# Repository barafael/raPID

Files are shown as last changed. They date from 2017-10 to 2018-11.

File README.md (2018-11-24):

# raPID: Rafaels PID flight controller



This flight controller consists mostly of a teensy 3.2 and an EM-SENtral motion sensor board. The
teensy can read up to 8 PWM or PPM channels from your standard RC receiver (see
include/pins.h for input/output pin numbers). Each of the outputs can be driven
by a weighted sum of the roll, pitch, yaw PID responses and the throttle
channel. The remaining 4 channels are currently unused, but it would be simple
to use them to drive the outputs like the throttle channel does. This is a
matrix multiplication, conceptually. The matrix maps an input (RX, PID) to the
output.

Three inputs drive the PID setpoints. By default, a cascaded PID controller is
used - resulting in stabilize mode. The first controller gets the RX input and
the absolute attitude from the IMU sensor. It outputs the desired rate. This
rate is fed as the setpoint to another controller, which uses the faster gyro
measurements of angular rate as process value. This setup results in
stabilization mode (stick deviation sets vehicle attitude). Acro mode is
achieved by disabling the first controller (which will then just pass through
the setpoint to the next controller) and only using the rate controller.

## Features
- [x] Arming/disarming
- [x] Mixers for each output, applying differently weighted inputs and IMU data to the outputs
- [x] Rate/stabilize mode
- [x] Support several output waveforms
  - [x] Various output classes (Servo, ESC, anyPWM)
  - [x] 400Hz update rate for ESCs using analogWrite timers (to do: test it)
  - [x] Arbitrary PWM waveform generation to drive even LEDs
- [x] PID Improvements
  - [x] D noise filters: lowpass, moving average
  - [x] Derivative-on-{error, feedback, setpoint}
  - [ ] Fixed point PID implementation
  - [ ] [not needed right now] Calculating error external from algorithm or pass an ```errorfunc(number, number) -> number``` function pointer (more general)

## TODO
- [x] Fix serial monitor ritual (current: remove tx, reboot, wait for sermon, connect tx)
- [x] Fix gyro vs. fused and rate vs. stbl issues (-15 factor)
- [ ] Receiver
  - [x] Per-channel offsets to set zero/mid-points and somehow work around special case for throttle, which needs 50% extra offset
  - [ ] Fix PPM receiver read
- Outputs
  - [x] 400Hz PWM output test and fix
  - [ ] Rethink set_limits, general implementation of generic waveforms? Specialization in servo (endpoints, expo?, trimming, inversion). Maximum range must be at least standard max signal pulse width
- [ ] Safety Enhancements
  - [x] Make sure arming functionality works and is reliable
  - [ ] Add safety mechanisms for receiver signal loss (detect RX failsafe output)
  - [ ] Fix/Improve watchdog timer functionality. Is this even necessary? A software crash will likely lead to crash of vehicle, since the controller boots to disarmed mode. Check if wakeup from watchdog, then proceeding armed? Currently, watchdog is disabled
- [x] Increase IMU sensor sampling rates - 1kHz

## Ideas
- [ ] Airspeed-adjustable gains
- [ ] Live coefficient tweaking (standard tx or telemetry hardware)
  - [ ] RFM95 lora board for config data, telemetry
- [x] IMU solution overhaul: Ultimate SENtral or other; constant sampling rate simplifies PID and makes theory on time-discrete systems applicable
  - [x] General IMU interface class to test different IMU implementations
- [ ] Matrix multiplication for output coefficients (every output is some weighted sum of the inputs + PID response) Possibly use DSP instructions and SIMD - one microsecond for multiplying 8x12 and a 12 column vector is achievable
  - [ ] Weights in output matrix are only linear multiplication. Would it make sense to use a matrix of function pointers to support expo? Performance (inlining possible?)?
  - [ ] 8x12 x 12x1 int16_t matrix/vector multiplication with naive for loop implementation: 12us. Unrolled loops: 3us-6us. Sufficient, probably.
  - [ ] 8x12 x 12x1 float matrix-vector multiplication with unrolled loops: 170us. Insufficient.
- [ ] Arbitrary flight modes (different PID settings, offsets, and I/O matrix)
- [ ] Flight mode interpolation (otherwise called transitional mixers) to smoothly switch between any two flight modes
  - [ ] Flight mode matrix to other flight mode matrix: ```(1 - transition) * old_mat + transition * new_mat``` for now. Sine/other functions, duration of transition, etc. later.
  - [ ] How to support more complex transitions where linear is insufficient? Pass pointer to function that takes end and start points, and percent, and gives interpolation value:
        ```squared_sine(startpoint, endpoint, percent) -> interpolated```
- [ ] Adjust settings wirelessly, ideally using a desktop application/website (have not thought about that part yet... far off)
- [ ] Use an RTOS?
  * Periodic tasks that run slower than flight loop:
    * Arming/disarming toggle check
    * Flightmode matrix transition update
    * Telemetry
    * Watchdog
    * RX update (depending on mode(PPM, PWM)) lower frequency than flight loop
    * RX check if has_channel (or use RC RX failsafe mode to detect?) [can run at 5Hz]
    * Serial debug output (?)
  * As fast as possible
    * IMU read
    * PID loops
    * Flight mode matrix vector multiplication
    * ```output.apply(value)```

Blog-in-progress @ [https://barafael.github.io/Remote-Control-Vehicle-Balance-controller/](https://barafael.github.io/Remote-Control-Vehicle-Balance-controller/)

## Inspiration and Acknowledgments

* OpenAeroVTOL from the RCGroups forums, by HappySundays - awesome project.
* Jeff Rowberg's MPU6050 library and example code.

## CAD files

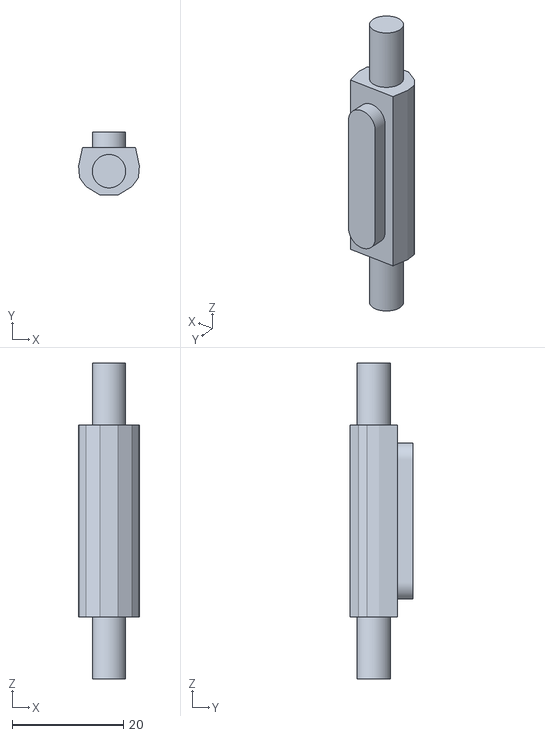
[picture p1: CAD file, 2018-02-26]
handle.stl
10.9 x 11.4 x 56.7

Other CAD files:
handle.blend

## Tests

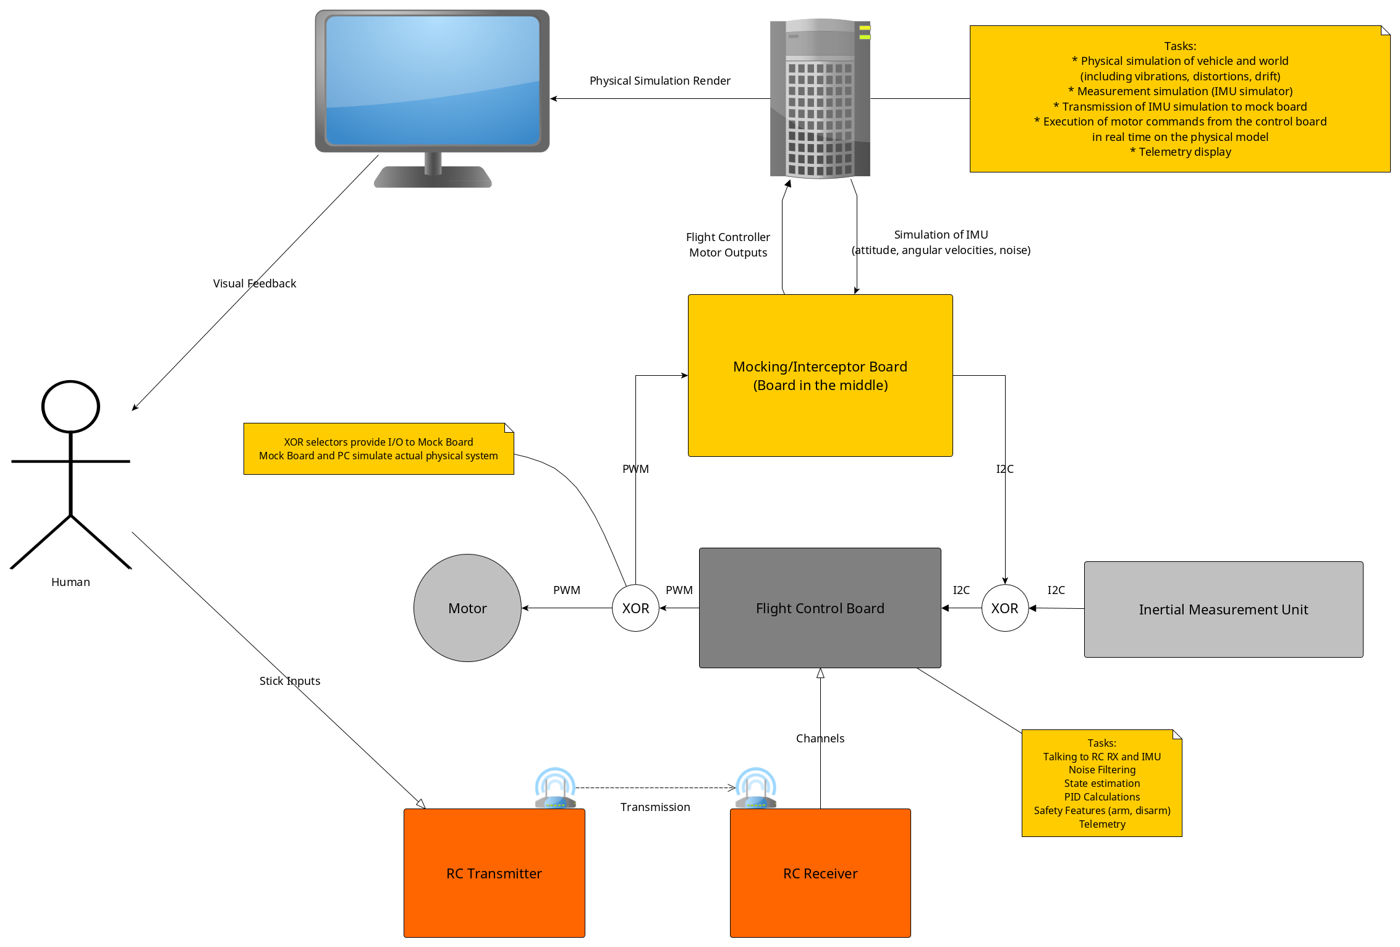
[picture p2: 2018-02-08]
controller_simulator_test_rig.png

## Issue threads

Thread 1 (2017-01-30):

Yaw readout drift [?]

barafael, 2017-01-30:
Yaw readout in Teensy_MPU6050_imu.ino is constantly increasing until it stabilizes after a while. Pitch and roll readouts are not affected. This could be a hardware issue, or a bug, or a wrong value set at   `mpu.setXGyroOffset(220);`
`mpu.setYGyroOffset(76);`
`mpu.setZGyroOffset(-85);`
`mpu.setZAccelOffset(1788);`

barafael, 2017-11-22:
https://www.i2cdevlib.com/forums/topic/10-why-is-the-dmp-yaw-stable/

Closed 2017-11-24.

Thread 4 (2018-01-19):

No need to wait after Wire.requestFrom()

Koepel, 2018-01-19:
In the file raPID/src/imu.cpp you can remove this line: `while (Wire.available() < 6) {}`. It is used twice.

The Wire.requestFrom() waits until the complete I2C transaction on the bus has finished. There is no need to wait for something after the call to Wire.requestFrom().
In case of a bus collision or an error that the Wire library could detect (it can not detect most problems), then the Wire.available() will probably return zero, and that loop will halt the sketch.

barafael, 2018-01-19:
Thanks for spotting that! I will remove the line. Awesome!

Koepel, 2018-01-19:
Thanks. That was fast.

You use the I2Cdev code, which is using the Wire library in a wrong way ( https://github.com/jrowberg/i2cdevlib/issues/265 ). That library is no longer maintained and the issues are piling up. The library is also a little outdated. Your copy of "init_mpu6050" is therefor also a little outdated. The FastWire option is not really needed and setting the TWBR for the speed is no longer needed, since there is a Wire.setClock() function now.

There is not much you or me can do about it. Keep in mind that the library is slower than needed, with extra unnecessary bus activity that slows it down. With the current version of the AVR Wire library the I2Cdev library works (despite the wrong use), so for now it is okay.

barafael, 2018-01-19:
I guess it would be possible to use the i2c_t3 library in I2Cdev, however as you said it could be a lot of work.

I have sufficient power on my microcontroller to be able to do my own sensor fusion, so [this library by Kris Winer](https://github.com/kriswiner/MPU6050) is worth looking at for me.
In the long run, I want to use a different sensor anyway, as InvenSense has presented really good new options as recent as CES.

Thank you for pointing out the issues!

Koepel, 2018-01-19:
You might consider to upgrade to the MPU-9250 and try the Kris Winer AHRS fusion. Sometimes a MPU-6050 module is shipped with a smaller capacitor which causes extra noise. The MPU-9250 doesn't have that capacitor.

barafael, 2018-01-19:
Ok, that sounds like it will improve the IMU quite a bit. I am wondering about the tradeoffs of using on-chip sensor fusion vs. doing it on the main board. I guess I will try both!

BTW, great job on helping all those other people use the Wire library correctly.

Closed 2018-01-19.

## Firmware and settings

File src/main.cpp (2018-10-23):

#include "Arduino.h"

#include <stdint.h>

//#define WATCHDOG

#include "../include/output/ESCOutput.hpp"
#include "../include/output/FastPWMOutput.hpp"
#include "../include/output/LEDOutput.hpp"
#include "../include/imu/axis.hpp"
#include "../include/pid/PIDController.hpp"
#include "../include/receiver/PWMReceiver.hpp"
#include "../include/receiver/PPMReceiver.hpp"
#include "../include/ArmingState.hpp"
#include "../include/error_blink.h"
#include "../include/pins.h"
#include "../include/imu/SENtralIMU.hpp"
#include "../include/settings.h"

#ifdef WATCHDOG
#include "../include/Watchdog.hpp"
#endif

#define TIMING_ANALYSIS
#ifdef TIMING_ANALYSIS
#define time(f)                          \
    {                                    \
        digitalWrite(DEBUG_PIN, HIGH);   \
        f;                               \
        digitalWrite(DEBUG_PIN, LOW);    \
    }
#else
#define time(f) f
#endif

#define notime(f) f


/*
   ----------------------------------------------
   ---             HARDWARE SETUP             ---
   ----------------------------------------------

   SENtral Breakout ----- Teensy 3.2
   3.3V ----------------- 15
   GND ------------------ 14
   SDA ------------------ A4/pin 18
   SCL ------------------ A5/pin 19
   INT ------------------ Digital Pin 6 (see pins.h)

   See ../include/pins.h for more pin definitions.
   */

/* Default start state */
state_t state = DISARMED;

/* Scaled yaw_pitch_roll to [0, 1000] */
//axis_t attitude = { 0, 0, 0 };
float attitude[3] = { 0 };

/* Angular Rate */
//axis_t angular_rates = { 0, 0, 0 };
float angular_rates[3] = { 0 };

float pid_output_roll_stbl = 0.0;
float pid_output_roll_rate = 0.0;

float pid_output_pitch_stbl = 0.0;
float pid_output_pitch_rate = 0.0;

float pid_output_yaw_rate = 0.0;

channels_t channels = { 0 };

static void print_attitude(axis_t attitude) {
    for (size_t index = 0; index < 3; index++) {
        Serial.print(attitude[index]);
        Serial.print(F("\t"));
    }
    Serial.println();
}

static void print_velocity(float *velocity) {
    for (size_t index = 0; index < 3; index++) {
        Serial.print(velocity[index]);
        Serial.print(F("\t"));
    }
    Serial.println();
}

static void print_velocity_max(axis_t velocity) {
    static int64_t max_velocity = 0;
    for (size_t index = 0; index < 3; index++) {
        if (velocity[index] > max_velocity || velocity[index] < -max_velocity) {
            max_velocity = velocity[index];
            Serial.println((long) max_velocity);
        }
    }
}

static void print_channels(channels_t channels) {
    for (size_t index = 0; index < NUM_CHANNELS; index++) {
        Serial.print(channels[index]);
        Serial.print(F("\t"));
    }
    Serial.println();
}

extern "C" int main(void) {
    pinMode(LED_PIN, OUTPUT);
    pinMode(DEBUG_PIN, OUTPUT);

    Serial.begin(9600);
    while(!Serial);

    int counter = 10;
    while(counter) {
        Serial.println("Hello");
        delay(500);
        digitalWrite(LED_PIN, !digitalRead(LED_PIN));
        counter--;
    }

    static bool blink_state = false;

    delay(1000);

    channels_t offsets = { -1000, -1500, -1500, -1500, -1500, -1500 };

    PWMReceiver receiver(THROTTLE_INPUT_PIN, ROLL_INPUT_PIN,
                         PITCH_INPUT_PIN,    YAW_INPUT_PIN,
                         AUX1_INPUT_PIN,     AUX2_INPUT_PIN,
                         offsets);
  
    //PPMReceiver receiver(23, offsets);

    while (!receiver.has_signal()) {
        delay(500);
        Serial.println(F("No receiver signal! Waiting."));
    }

    Serial.println(F("Receiver signal detected, continuing."));

    PIDParams roll_param_stbl ( 2.0 , 0.0 , 0.0 , 12.0 , 400.0);
    PIDParams roll_param_rate ( 0.65 , 0.0 , 0.0 , 12.0 , 400.0);

    PIDParams pitch_param_stbl( 2.0 , 0.0 , 0.0 , 12.0 , 400.0);
    PIDParams pitch_param_rate( 0.65 , 0.0 , 0.0 , 12.0 , 400.0);

    PIDParams yaw_param_rate  ( 1.5 , 0.0 , 0.0 , 12.0 , 400.0);

    PIDController roll_controller_stbl(roll_param_stbl);
    PIDController roll_controller_rate(roll_param_rate);

    PIDController pitch_controller_stbl(pitch_param_stbl);
    PIDController pitch_controller_rate(pitch_param_rate);

    PIDController yaw_controller_rate(yaw_param_rate);

    FastPWMOutput back_left_out_mixer  (LEFT_SERVO_PIN  , 1.0 , -1.0 , -1.0 , 1.0);
    FastPWMOutput back_right_out_mixer (RIGHT_SERVO_PIN , 1.0 , 1.0  , -1.0 , -1.0);
    FastPWMOutput front_left_out_mixer (FRONT_SERVO_PIN , 1.0 , -1.0 , 1.0  , -1.0);
    FastPWMOutput front_right_out_mixer(BACK_SERVO_PIN  , 1.0 , 1.0  , 1.0  , 1.0);

    back_left_out_mixer  .shut_off();
    back_right_out_mixer .shut_off();
    front_left_out_mixer .shut_off();
    front_right_out_mixer.shut_off();

    roll_controller_stbl.set_enabled(true);
    roll_controller_rate.set_enabled(true);

    pitch_controller_stbl.set_enabled(true);
    pitch_controller_rate.set_enabled(true);

    SENtralIMU sentral;

#ifdef WATCHDOG
    Watchdog dog;
#endif

    ArmingState arming_state(channels);

    /* Flight loop */
    while(true) {
        receiver.update(channels);
        //print_channels(channels);

        sentral.update_attitude(attitude);
        //print_attitude(attitude);

        sentral.update_angular_rates(angular_rates);
        //print_velocity(angular_rates);

        switch (arming_state.get_state()) {
            case ARMED:
                pid_output_roll_stbl = roll_controller_stbl.  compute(attitude[ROLL_AXIS], channels[ROLL_CHANNEL]);

                pid_output_roll_rate = roll_controller_rate.  compute(angular_rates[ROLL_AXIS], -pid_output_roll_stbl);

                //pitch_controller_stbl.set_p((channels[ROLL_CHANNEL] + 500) * (15.0 / 1000));
                //pitch_controller_stbl.set_i((channels[YAW_CHANNEL]  + 500) * (5.0  / 1000));

                //Serial.println(pitch_controller_stbl.get_p());
                //Serial.print("\t");
                //Serial.println(pitch_controller_stbl.get_d());

                pid_output_pitch_stbl = pitch_controller_stbl.compute(attitude[PITCH_AXIS], channels[PITCH_CHANNEL] / 10);

                pid_output_pitch_rate = pitch_controller_rate.compute(angular_rates[PITCH_AXIS], -pid_output_pitch_stbl);

                /* Yaw needs rate only - yaw stick controls rate of rotation, there is no fixed reference */
                pid_output_yaw_rate = yaw_controller_rate.    compute(angular_rates[YAW_AXIS], channels[YAW_CHANNEL]);

                back_left_out_mixer  .apply(channels[THROTTLE_CHANNEL], pid_output_roll_rate, pid_output_pitch_rate, pid_output_yaw_rate);
                back_right_out_mixer .apply(channels[THROTTLE_CHANNEL], pid_output_roll_rate, pid_output_pitch_rate, pid_output_yaw_rate);
                front_left_out_mixer .apply(channels[THROTTLE_CHANNEL], pid_output_roll_rate, pid_output_pitch_rate, pid_output_yaw_rate);
                front_right_out_mixer.apply(channels[THROTTLE_CHANNEL], pid_output_roll_rate, pid_output_pitch_rate, pid_output_yaw_rate);

                //#define DEBUG_COL
#ifdef DEBUG_COL
                Serial.print(F("setp:"));
                Serial.print(channels[ROLL_CHANNEL]);
                Serial.print(F("\troll-angl:"));
                Serial.print(attitude[ROLL_AXIS]);
                Serial.print(F("\tpid_output_roll_stbl:"));
                Serial.print(pid_output_roll_stbl);
                Serial.print(F("\tpid_output_roll_rate:"));
                Serial.println(pid_output_roll_rate);
#endif

                break;

            case DISARMED:
                back_left_out_mixer  .shut_off();
                back_right_out_mixer .shut_off();
                front_left_out_mixer .shut_off();
                front_right_out_mixer.shut_off();

                break;

            default:
                Serial.println(F("Unimplemented state! Will disarm."));
                state = DISARMED;
                break;
        }

        /* Blink LED to indicate activity */
        blink_state = !blink_state;
        digitalWrite(LED_PIN, blink_state);
#ifdef WATCHDOG
        dog.feed();
#endif
    }
}

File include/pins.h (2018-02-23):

#ifndef PINS_H
#define PINS_H

#include <stdint.h>

static const uint8_t DEBUG_PIN = 15;

static const uint8_t LED_PIN = 15;

static const uint8_t SENTRAL_GND = 13;
static const uint8_t SENTRAL_POWER = 14;

static const uint8_t SENTRAL_INTERRUPT_PIN = 8;

typedef enum {
    THROTTLE_INPUT_PIN = 22,
    ROLL_INPUT_PIN     = 20,
    PITCH_INPUT_PIN    = 21,
    YAW_INPUT_PIN      = 23,
    AUX1_INPUT_PIN     = 19,
    AUX2_INPUT_PIN     = 18,
} input_pin;

typedef enum {
    LEFT_SERVO_PIN  = 5,
    RIGHT_SERVO_PIN = 4,
    FRONT_SERVO_PIN = 3,
    BACK_SERVO_PIN  = 6
} output_pin;

#endif // PINS_H

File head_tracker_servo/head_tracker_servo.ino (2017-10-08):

/* ============================================
  I2Cdev device library code is placed under the MIT license
  Copyright (c) 2012 Jeff Rowberg

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
  THE SOFTWARE IS PROVIDED "AS IS", WITHOUT WARRANTY OF ANY KIND, EXPRESS OR
  IMPLIED, INCLUDING BUT NOT LIMITED TO THE WARRANTIES OF MERCHANTABILITY,
  FITNESS FOR A PARTICULAR PURPOSE AND NONINFRINGEMENT. IN NO EVENT SHALL THE
  AUTHORS OR COPYRIGHT HOLDERS BE LIABLE FOR ANY CLAIM, DAMAGES OR OTHER
  LIABILITY, WHETHER IN AN ACTION OF CONTRACT, TORT OR OTHERWISE, ARISING FROM,
  OUT OF OR IN CONNECTION WITH THE SOFTWARE OR THE USE OR OTHER DEALINGS IN
  THE SOFTWARE.
  ===============================================
*/

/* I2C device class (I2Cdev) demonstration Arduino sketch for MPU6050 class using DMP (MotionApps v2.0)
  6/21/2012 by Jeff Rowberg <jeff@rowberg.net>
  Updates should (hopefully) always be available at https://github.com/jrowberg/i2cdevlib

  Changelog:
      2013-05-08 - added seamless Fastwire support
                 - added note about gyro calibration
      2012-06-21 - added note about Arduino 1.0.1 + Leonardo compatibility error
      2012-06-20 - improved FIFO overflow handling and simplified read process
      2012-06-19 - completely rearranged DMP initialization code and simplification
      2012-06-13 - pull gyro and accel data from FIFO packet instead of reading directly
      2012-06-09 - fix broken FIFO read sequence and change interrupt detection to RISING
      2012-06-05 - add gravity-compensated initial reference frame acceleration output
                 - add 3D math helper file to DMP6 example sketch
                 - add Euler output and Yaw/Pitch/Roll output formats
      2012-06-04 - remove accel offset clearing for better results (thanks Sungon Lee)
      2012-06-01 - fixed gyro sensitivity to be 2000 deg/sec instead of 250
      2012-05-30 - basic DMP initialization working

      2017-01-10 - [Rafael Bachmann] add servo output (needs low pass filter such as capacitor in parallel for pwm to work)
      2017-01-30 - [Rafael Bachmann] modifications to run this sketch on the teensy 3.2
      2017-01-30 - [Rafael Bachmann] removal of teapot output
      2017-09-10 - [Rafael Bachmann] boil down to head tracker implementation with 0-calibration
*/

// I2Cdev and MPU6050 must be installed as libraries, or else the .cpp/.h files
// for both classes must be in the include path of your project
#include "I2Cdev.h"

#include "MPU6050_6Axis_MotionApps20.h"
//#include "MPU6050.h" // not necessary if using MotionApps include file

#include <Servo.h>
Servo yaw_servo;
Servo pitch_servo;

// Arduino Wire library is required if I2Cdev I2CDEV_ARDUINO_WIRE implementation
// is used in I2Cdev.h
#if I2CDEV_IMPLEMENTATION == I2CDEV_ARDUINO_WIRE
#include "Wire.h"
#endif

// class default I2C address is 0x68
// specific I2C addresses may be passed as a parameter here
// AD0 low = 0x68 (default for SparkFun breakout and InvenSense evaluation board)
// AD0 high = 0x69
MPU6050 mpu;
//MPU6050 mpu(0x69); // <-- use for AD0 high

/* =========================================================================
   NOTE: In addition to connection 3.3v, GND, SDA, and SCL, this sketch
   depends on the MPU-6050's INT pin being connected to the Teensy's digital pin 2.

   HARDWARE SETUP:
     MPU6050 Breakout ----- Teensy 3.2
     3.3V ----------------- 3.3V
     GND ------------------ GND
     SDA ------------------ A4/pin 18
     SCL ------------------ A5/pin 19
     INT ------------------ Digital Pin 2 (Teensy)
   ========================================================================= */
/* =========================================================================
   NOTE: For calibration, connect a push-to-make-contact push button to ground and
   $(CALIBRATION_PIN) (pin 14). Push button to reset the camera to initial position.
   Issue: when yaw drifts over or is pushed to the limit (180) by calibration,
   servo range is strongly limited in one direction and flips around.

   ========================================================================= */

#define YAW_SERVO_PIN 10
#define PITCH_SERVO_PIN 11

#define CALIBRATION_PIN 14

// Calibration variables
float yaw_offset = 0;
float pitch_offset = 0;


#define LED_PIN 13 // (Arduino is 13, Teensy 3.2 is 13, Teensy++ is 6)
bool blinkState = false;


// MPU control/status vars
bool dmpReady = false;  // set true if DMP init was successful
uint8_t mpuIntStatus;   // holds actual interrupt status byte from MPU
uint8_t devStatus;      // return status after each device operation (0 = success, !0 = error)
uint16_t packetSize;    // expected DMP packet size (default is 42 bytes)
uint16_t fifoCount;     // count of all bytes currently in FIFO
uint8_t fifoBuffer[64]; // FIFO storage buffer

// orientation/motion vars
Quaternion q;           // [w, x, y, z]         quaternion container
VectorInt16 aa;         // [x, y, z]            accel sensor measurements
VectorInt16 aaReal;     // [x, y, z]            gravity-free accel sensor measurements
VectorInt16 aaWorld;    // [x, y, z]            world-frame accel sensor measurements
VectorFloat gravity;    // [x, y, z]            gravity vector
float euler[3];         // [psi, theta, phi]    Euler angle container
float ypr[3];           // [yaw, pitch, roll]   yaw/pitch/roll container and gravity vector

// ================================================================
// ===               INTERRUPT DETECTION ROUTINE                ===
// ================================================================

volatile bool mpuInterrupt = false;     // indicates whether MPU interrupt pin has gone high
void dmpDataReady() {
  mpuInterrupt = true;
}

// ================================================================
// ===                      INITIAL SETUP                       ===
// ================================================================
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

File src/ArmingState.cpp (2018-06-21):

#include "../include/ArmingState.hpp"

ArmingState *arming_state_instance = nullptr;

static const bool state_transition_triggered(channels_t input) {
    if (input[THROTTLE_CHANNEL] >   55) return false;
    if (input[ROLL_CHANNEL]     <  445) return false;
    /* No typo - roll is different from the other channels when not inverted */
    if (input[PITCH_CHANNEL]    > -445) return false;
    if (input[YAW_CHANNEL]      > -445) return false;
    return true;
}

static const bool arming_debug = true;

// #define ARMING_DEBUG

void update_state() {
    bool triggered = state_transition_triggered(arming_state_instance->channels);
    switch (arming_state_instance->internal_state) {
        case ARMED:
#ifdef ARMING_DEBUG
            Serial.println("Armed");
#endif
            if (triggered) {
                arming_state_instance->internal_state    = DISARMING;
                arming_state_instance->state_change_time = millis();
            }
            break;

        case DISARMED:
#ifdef ARMING_DEBUG
            Serial.println("Disarmed");
#endif
            if (triggered) {
                arming_state_instance->internal_state    = ARMING;
                arming_state_instance->state_change_time = millis();
            }
            break;

        case DISARMING:
            if (triggered) {
#ifdef ARMING_DEBUG
                Serial.println("Disarming");
#endif
                if ((millis() - arming_state_instance->state_change_time) > arming_state_instance->DISARM_TIMEOUT_MS) {
                    arming_state_instance->internal_state = DISARMING_STANDBY;
                } else
                    break;
            } else {
#ifdef ARMING_DEBUG
                Serial.println("Going back to armed");
#endif
                arming_state_instance->internal_state = ARMED;
            }
            break;

        case DISARMING_STANDBY:
            if (triggered) {
#ifdef ARMING_DEBUG
                Serial.println("Release the hold to complete disarming!");
#endif
            } else {
                arming_state_instance->internal_state = DISARMED;
            }
            break;

        case ARMING:
#ifdef ARMING_DEBUG
            Serial.println("Arming");
#endif
            if (triggered) {
                if ((millis() - arming_state_instance->state_change_time) > arming_state_instance->ARM_TIMEOUT_MS) {
                    arming_state_instance->internal_state = ARMING_STANDBY;
                } else
                    break;
            } else {
#ifdef ARMING_DEBUG
                Serial.println("Going back to disarmed");
#endif
                arming_state_instance->internal_state = DISARMED;
            }
            break;

        case ARMING_STANDBY:
            if (triggered) {
#ifdef ARMING_DEBUG
                Serial.println("Release the hold to complete arming!");
#endif
            } else {
                arming_state_instance->internal_state = ARMED;
            }
            break;

            /* unimplemented state? */
        default:
#ifdef ARMING_DEBUG
            Serial.println("Unimpl. Disarmed now!");
#endif
            arming_state_instance->internal_state = DISARMED;
    }
}

ArmingState::ArmingState(channels_t channels) : channels(channels) {
    arming_state_instance = this;
    if (!state_change_timer.begin(update_state, INTERVAL_US)) {
        error_blink(STATE_TIMER_HARDWARE_BUSY, "Could not set up interval timer for arming state update!");
    }
}

const state_t ArmingState::get_state() {
    noInterrupts();
    switch (internal_state) {
        case ARMED:
        case DISARMING:
        case DISARMING_STANDBY: interrupts(); return ARMED;
        case DISARMED:
        case ARMING:
        case ARMING_STANDBY: interrupts(); return DISARMED;
    }
    interrupts();
    return DISARMED;
}

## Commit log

2017-01-30 add basic starting point for IMU
2017-01-30 add libraries necessary for teensy IMU sketch
2017-01-30 add description and GH link for basic IMU sketch
2017-09-10 add head tracker
    (*.ino for teensy 3.2)
2017-09-10 add calibration functionality
2017-10-08 servo output
2017-10-08 limit servo positions
2017-10-08 receiver 'pwm' interrupt read
2017-10-30 read receiver and IMU in one sketch
2017-10-31 add error handling
    fancy blinking led error codes for 'ease of use'
2017-10-31 complete head tracker implementation
    hardware (PCB) is on the way!
2017-10-31 implementation of ONLY IMU for teensy 3.2
2017-10-31 work on PID loop for one axis
2017-10-31 add hardware fritzing files
    [Receiver.fzz, Transmitter.fzz]
2017-11-01 add auto-calibration
2017-11-02 work-in-progress pid loop on the absolute attitude
2017-11-03 use double instead of float for pid variables
2017-11-03 add pid calculation based on rate
    instead of absolute angle. Currently unused.
2017-11-11 remove head tracker from repo
    [Receiver.fzz, Transmitter.fzz]
2017-11-11 remove teensy_IMU code from repo
2017-11-19 adjust pid coefficients
2017-11-19 debug printing
2017-11-20 move pin definitions to pins
2017-11-20 add teensy headers
2017-11-20 add teensy tools
2017-11-20 attempt at getting interrupts to work
2017-11-20 set IMU interrupt pin as input
    worked before when using arduino ide
2017-11-21 remove unused teensy stdlib files
2017-11-21 add schematic v0
    [raPID_FC.fzz]
2017-11-21 add switch and poti
    [raPID_FC.fzz]
2017-11-22 add debug pins and through-holes
    [raPID_FC.fzz]
2017-11-22 move mpu interrupt pin to d12
2017-11-22 headerize imu
2017-11-22 headerize pid calculation
2017-11-23 toggle led not debug
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2017-11-23 use pid rate loop in main loop
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2017-11-24 update calibration offsets for this board
2017-11-24 dual loops implementation
    rate/stabilize
    [imu.cpp, main.cpp]
2017-11-25 add pid coefficient structure
2017-11-25 servo low on disarm
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2017-11-26 add mini version of FC board
    [raPID_FC_mini.fzz]
2017-11-27 update pcb design
    [raPID_FC.fzz, raPID_FC_mini.fzz]
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2017-12-09 improve mini board
    [raPID_FC_mini.fzz]
2017-12-11 work on circuit diagram
    [raPID_FC.fzz, raPID_FC_mini.fzz]
2017-12-24 better names for gyro_axis
2017-12-25 move imutype to imu.h
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2017-12-25 intern-ify pid response variables
2017-12-25 add better modular pid controller implementation
    based on the notes from Brett Beauregard in his piece 'improving the beginner's PID'
2017-12-26 pitch output additional to roll output
2018-01-01 use actual output for pid
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2018-01-04 add mounting holes
    [raPID_FC_mini.fzz]
2018-01-04 remove superfluous pid struct definition
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2018-01-04 use new pid implementation
2018-01-05 update mini board
    [raPID_FC_mini.fzz]
2018-01-05 remove old pid implementation
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2018-01-06 change debug pin to not overlap with servo output
2018-01-06 move imu index struct
2018-01-06 fix serial output
    by adding 2s delay...
    [main.cpp]
2018-01-07 use WIP OOP receiver implementation
    just because it compiles it doesn't mean it works
    [main.cpp, settings.h]
2018-01-07 adjust pins for mini board
2018-01-08 Use current directory as source
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2018-01-16 add support for teensy35 platform
2018-01-17 add output inversion prototype
2018-01-17 logical throttle separate from writeMicroseconds time
2018-01-18 correct pin doc
2018-01-19 use 0-centered measurements for receiver and IMU
2018-01-19 remove calls to Wire.available spotted by Koepel
    https://github.com/barafael/raPID/issues/4
    [imu.cpp]
2018-01-19 add timing pin toggle
2018-01-26 add teensy 3.5 fc board with 9250 and ms2511
    [rapid_fc_3.5.fzz]
2018-01-27 Update mini 3.2 board
    [raPID_FC_mini.fzz]
2018-01-27 update pin definitions for new hardware
2018-01-27 3.5 board
    [rapid_fc_3.5.fzz]
2018-01-28 fix dis/arming when roll not inverted
    [main.cpp]
2018-01-28 set imu calibration offsets
2018-01-28 set PID for miniquad
2018-01-29 add a couple todo's
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2018-01-29 add toggle for low throttle cutoff
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2018-02-01 rework arming system
    periodic timer task asynchronously updates internal state, which then is polled from flight loop
    [main.cpp, settings.h]
2018-02-01 improve names for pwm receiver array
2018-02-01 remove 'now' argument from PID compute function
2018-02-01 Add explicit cascaded pid implementation
2018-02-01 Improve filter implementation
    Filter superclass, private implementation details
2018-02-02 add conditional warning output
    please please remove before flying - it runs in interrupt routine.
2018-02-02 init instance pointer before activating interrupt
    nullptr deref possible
2018-02-02 generify pid controller to test fixed point math
    [main.cpp]
2018-02-02 Use initializer list for pwmreceiver interrupt handling
2018-02-03 remove calibration, better done statically
2018-02-03 imu has class now
2018-02-03 return pwmreceiver to old implementation
2018-02-03 add function to find maximum velocity
2018-02-04 Fix arm/disarm
2018-02-04 add note about watchdog timer
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2018-02-07 add broken filter implementation
2018-02-08 fix derivative filter implementation
2018-02-08 disable teensy35 toolchain for now
2018-02-08 add schematic of hardware test rig idea
2018-02-09 fix pid timing control
2018-02-14 fix clamping receiver output
    [main.cpp]
2018-02-14 fix filter initialization
2018-02-15 add standby states to prevent state hopping
    if continuously triggered, state would jump between armed and disarmed
    every couple seconds. Now, trigger has to be released to enter new
    state.
    [ArmingState.cpp]
2018-02-15 fix fast pwm output
    [FastPWMOutput.cpp]
2018-02-16 prevent data race in arming function
    [ArmingState.cpp]
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2018-02-20 move imu to hardwareImu
2018-02-20 add raw imu interface
2018-02-20 add software imu interface
2018-02-20 add software madgwick filter
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2018-02-20 add sentral implementation
    i2c_t3 conflicts with wire.h, so remove mpu6050
2018-02-21 add board for flame frame
    [flame_frame_2.fzz]
2018-02-21 fix oop sentral interface
    [SENtralIMU.cpp]
2018-02-21 fix includes
    also fix build
    [main.cpp]
2018-02-22 improve sentral sensor interface
2018-02-22 move sentral pin definitions to pins.h
2018-02-26 Add handle for miniquad
    [handle.blend]
2018-02-26 Add handle STL
    [handle.stl]
2018-03-03 add getters for pid gains
2018-03-03 set acc and gyro frequencies to 1kHz
2018-03-04 replace pointers with references
    in some places where it is possible
    [SENtralIMU.cpp]
2018-03-05 embrace the float (for now)
    use fixed point later
    [SENtralIMU.cpp, main.cpp]
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2018-03-11 Remove explicit 2-stage cascaded pid controller
2018-03-29 Add f450 frame
    [flame_frame_3.fzz]
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2018-06-21 fix minor linter complaints
    [ArmingState.cpp, FastPWMOutput.cpp, ServoOutput.cpp]
2018-11-17 skip sonar scanner
    build succeeds but sonar scan fails with java exception
